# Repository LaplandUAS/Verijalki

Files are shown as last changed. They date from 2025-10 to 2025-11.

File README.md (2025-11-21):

# Blood trail drone
The blood trail demonstrator is developed for evaluating the feasibility of drone technology in the field of training hunting dogs, by leaving a blood trail from a reservoir for the hunting dogs to tracks without contaminating the trails with traces of the trainer's presence during the formation of the training trail.

## Equipment
* [DJI Mavic Pro](https://www.dji.com/fi/support/product/mavic)
* [Arduino Nano](https://store.arduino.cc/products/arduino-nano)
* 250mL syringe
* Steel compression spring
* 5-6V DC Peristatic pump
* UART Transciever modules 2X
* [Motor driver circuit](https://github.com/LaplandUAS/Verijalki/tree/main/pcb)
* [3D printed parts and accessories](https://github.com/LaplandUAS/Verijalki/tree/main/cad)

## Mechatronics
The demonstrator's mechatronics consist of a drone-mounted liquid payload dispenser, which is built of a spring loaded 250mL syringe, terminated with a peristatic pump for flow control. The syringe stays pressurised under the compression spring, and a peristatic pump is both used as a valve, and a method to mitigate clogs caused by blood coagulation and the low viscosity of anti-caking and anti-coagulation additives in low temperatures. The compression spring inhibits air from being pulled back into the payload.

## Electronics
The pump's flow rate is controlled wirelessly utilizing a pair of [HC-12](https://www.allaboutcircuits.com/projects/understanding-and-implementing-the-hc-12-wireless-transceiver-module/) Transciever modules. Any other UART-based transcievers that operate in a completely transparent mode can be used without extra configuration. The transmitter's signal is decoded from serial by an Atmega168 microcontroller onboard the motor driver, which translates the signal to match the pump's flow rate issued by the transmitter via an H-bridge IC. The transmitter device consists of an Arduino Nano, a control potentiometer, a matching HC-12 transciever and a battery pack. The motor controller is also capable of transmitting a callback signal indicating the payload depletion once an embedded magnet in the syringe trips a reed-switch placed at the level of depletion on the syringe body.

Either a separate battery pack, or an USB breakout board can be used to power the control circuit on board the drone. The Mavic Pro's add-on port uses a basic micro-USB connector in the following pin configuration:
| Micro-USB Pin  | Label |
| --- |:---:|
| 1 | GND  |
| 2 | 5V |
| 3 | 1.5V |
| 4 |? |
| 5 |? |

> [!CAUTION]
> The DJI Mavic pro doesn't follow any USB standard for it's add-on port. Use third party devices on this port at your own risk!

Only pins `1 & 2` are necessary for this application.

-----
<picture>
  <source media="(prefers-color-scheme: dark)" srcset="/img/logot/license.png">
  <source media="(prefers-color-scheme: light)" srcset="/img/logot/license_lightmode.png">
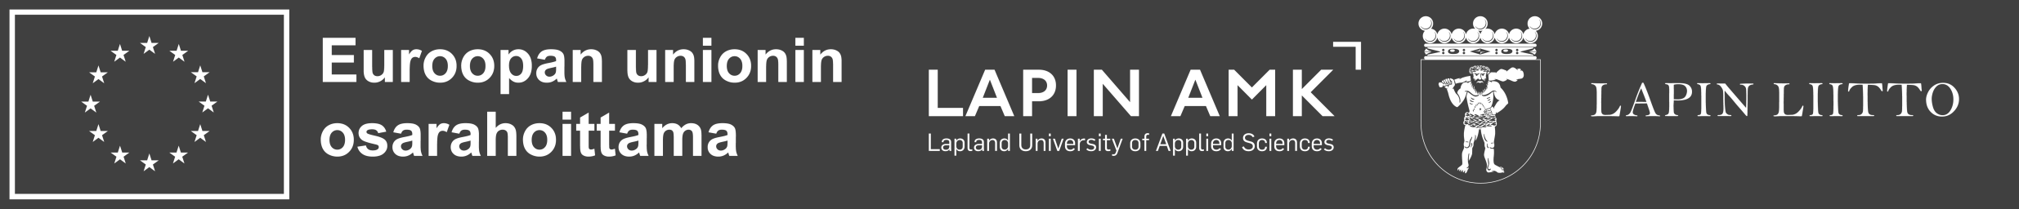
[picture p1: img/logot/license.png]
License logo
  
</picture>

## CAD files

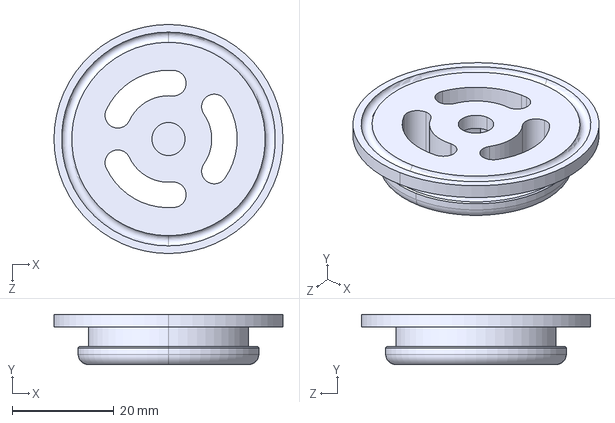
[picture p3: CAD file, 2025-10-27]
cad/drone/PlungerRetainer.STEP
45.0 x 9.85 x 45.0 mm

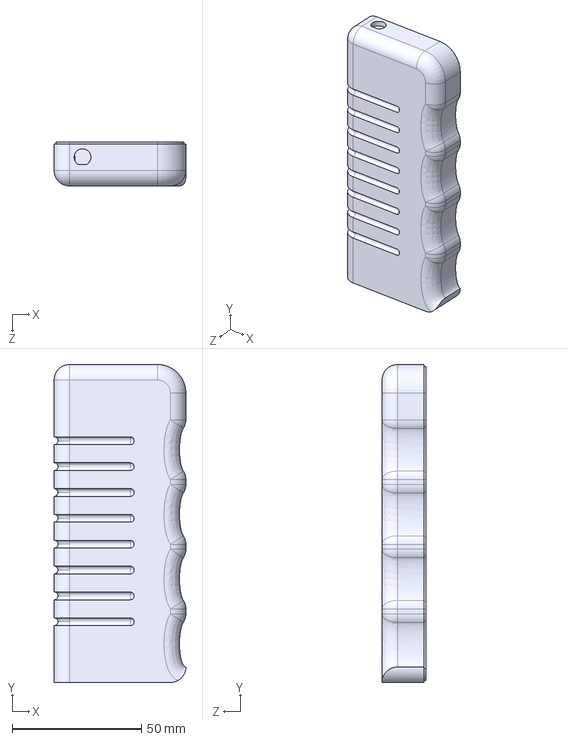
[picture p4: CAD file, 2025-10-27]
cad/ohjain/ShellBottom.STEP
51.0 x 123.0 x 17.0 mm

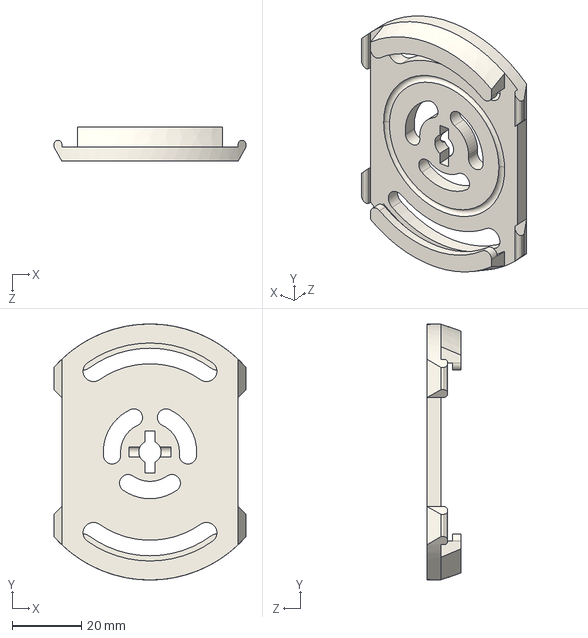
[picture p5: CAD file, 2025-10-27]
cad/drone/CylinderCapSpringRetainer.STEP
55.5 x 74.0 x 9.84 mm

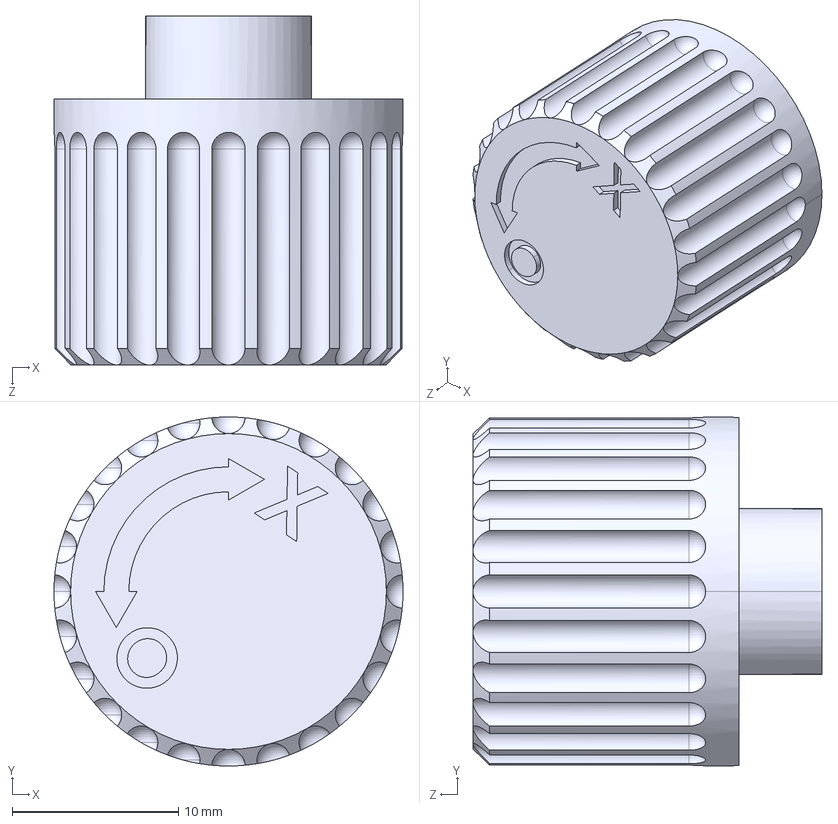
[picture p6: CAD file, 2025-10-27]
cad/ohjain/Knob.STEP
21.0 x 21.0 x 21.0 mm

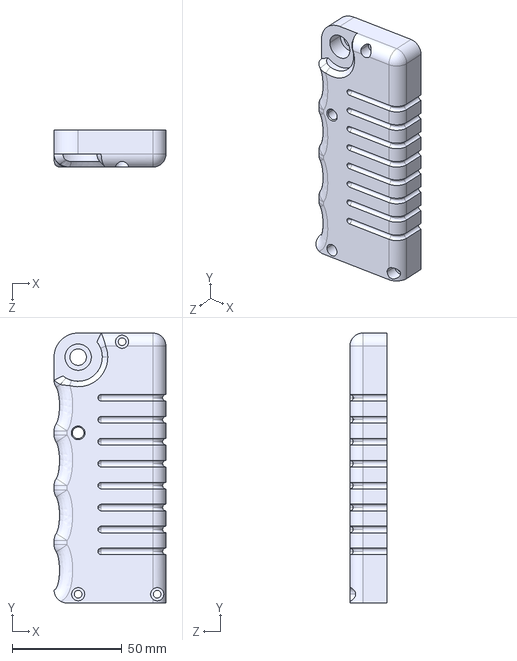
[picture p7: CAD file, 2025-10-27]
cad/ohjain/ShellTop.STEP
51.0 x 123.0 x 17.0 mm

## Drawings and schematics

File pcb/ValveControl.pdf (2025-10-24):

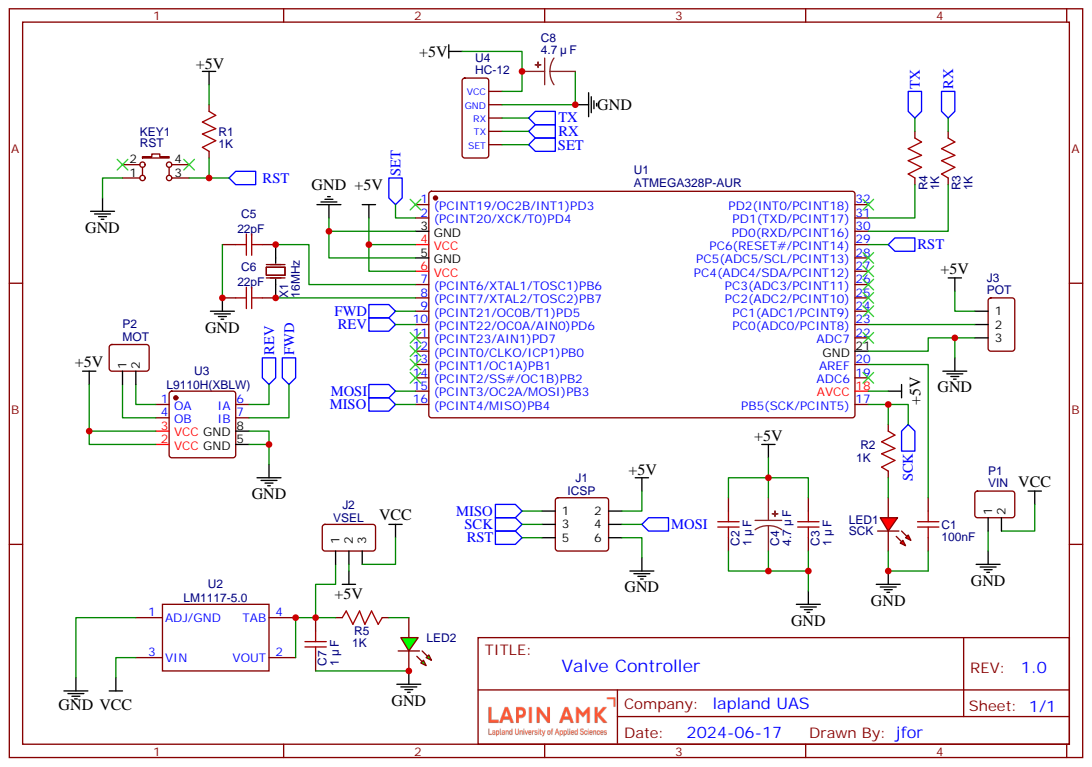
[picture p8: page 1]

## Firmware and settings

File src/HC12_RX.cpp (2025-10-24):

#include <Arduino.h>

#define THRESHOLD 5

#define FEEDBACK_PIN A0
#define SET 4
#define MOT_HIGH 5
#define MOT_LOW 6

uint8_t val = 0;

unsigned long lastSerialTime = 0;
const unsigned long timeout = 100; // ms — stop motor if no input in this time

// PWM timing
const unsigned long pwmPeriod = 10; // 10ms period = 100Hz
unsigned long pwmStart = 0;
bool motorOn = false;

void setup() {
  Serial.begin(9600);
  pinMode(FEEDBACK_PIN, INPUT);
  pinMode(MOT_HIGH, OUTPUT);
  pinMode(MOT_LOW, OUTPUT);
  StopMotor();
}

void loop() {
  unsigned long now = millis();

  // --- Read serial input ---
  if (Serial.available() > 0) {
    val = Serial.read();
    lastSerialTime = now;
  }

  // --- Run PWM motor control ---
  if ((now - lastSerialTime) < timeout && val > THRESHOLD) {
    updateMotorPWM(val, now);
  } else {
    StopMotor();
  }

  // --- Feedback signal ---
  if (digitalRead(FEEDBACK_PIN)) {
    Serial.println("MX");
  }
}

void updateMotorPWM(uint8_t pulse, unsigned long now) {
  float duty = pulse / 255.0;
  unsigned long onTime = pwmPeriod * duty;
  unsigned long offTime = pwmPeriod - onTime;

  unsigned long elapsed = now - pwmStart;

  if (!motorOn && elapsed >= offTime) {
    // Turn motor ON
    digitalWrite(MOT_HIGH, HIGH);
    digitalWrite(MOT_LOW, LOW);
    pwmStart = now;
    motorOn = true;
  } else if (motorOn && elapsed >= onTime) {
    // Turn motor OFF
    digitalWrite(MOT_HIGH, LOW);
    digitalWrite(MOT_LOW, LOW);
    pwmStart = now;
    motorOn = false;
  }
}

void StopMotor() {
  digitalWrite(MOT_HIGH, LOW);
  digitalWrite(MOT_LOW, LOW);
  motorOn = false;
}

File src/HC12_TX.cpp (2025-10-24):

#include <Arduino.h>

#define POT A0
#define LED 12
#define LDX 3
#define SET 2

String val;

void setup() {
  pinMode(LED,OUTPUT);
  pinMode(LDX,OUTPUT);
  pinMode(SET,OUTPUT);
  digitalWrite(LDX,LOW);
  digitalWrite(SET,HIGH);
  delay(80);
  Serial.begin(9600);
  digitalWrite(LED,HIGH);
}

void loop() {
if (Serial.available() > 0) {
  String val = Serial.readStringUntil('\n');  // or '\r' depending on sender
  val.trim();
  if (val == "MX") {
    digitalWrite(LDX, HIGH);
  }
}
  Serial.write(map(analogRead(POT),0,1023,0,255));
  delay(125);
}
